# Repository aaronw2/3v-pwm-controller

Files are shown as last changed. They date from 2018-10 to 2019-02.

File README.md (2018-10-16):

# 3v-pwm-controller
An Arduino M0 PWM controller with 3 mosfets designed to perform PWM at 3V
with a 3A 3V supply

This PWM controller provides 3 PWM channels designed to source and sink current.
The PWM signals are configured as an H-bridge with 6 GPIO pins controlling it.
One set of GPIO pins controlls the P-channel mosfets and another set controls
the N-channel mosfets.

Do not pull the P-channel mosfets low while pulling the attached N-channel
mosfet high! This will create a short and cause the 3V power supply to
overheat anb hopefully shut down! Bad things happen!

If you can't control both N and P channels simultaneously, set the P-channel
high and the N-channel low as an intermediate step.

PW0: P-channel = PA02, N-channel = PA05
PW1: P-channel = PA01, N-channel = PA04
PW2: P-channel = PA00, N-channel = PA03

For example, to pull PW0 high and PW1 low and PW2 high impedence (open),
set PA02 low, PA05 low, PA01 high, PA04 high, PA00 high, PA03 low.

The 3V supply is capable of providing up to 3A of current and is designed
to be powered by a 5V supply.

Each PWM channel should be able to handle at least 3A of current at 3V.
The MOSFETs are rated at over 5A each.

J1:
1: +5V
2: +5V
3: PWM0 GNR controlled by pulling PA05 high, +3 controlled by pulling PA02 low
4: PA08
5: PWM1 GND controlled by pulling PA04 high, +3 controlled by pulling PA01 low
6: PA09
7: PWM2 GND controlled by pulling PA03 high, +3 controlled by pulling PA00 low
8: PA10
9: +3V
10: +3V
11: GND
12: GND

J2:
1: D_P (D+) USB signal
2: D_N (D-) USB signal
3: PA22
4: PA21
5: PA19
6: PA18
7: +3V
8: GND

J3:
1: +5V
2: GND

SW1: Reset

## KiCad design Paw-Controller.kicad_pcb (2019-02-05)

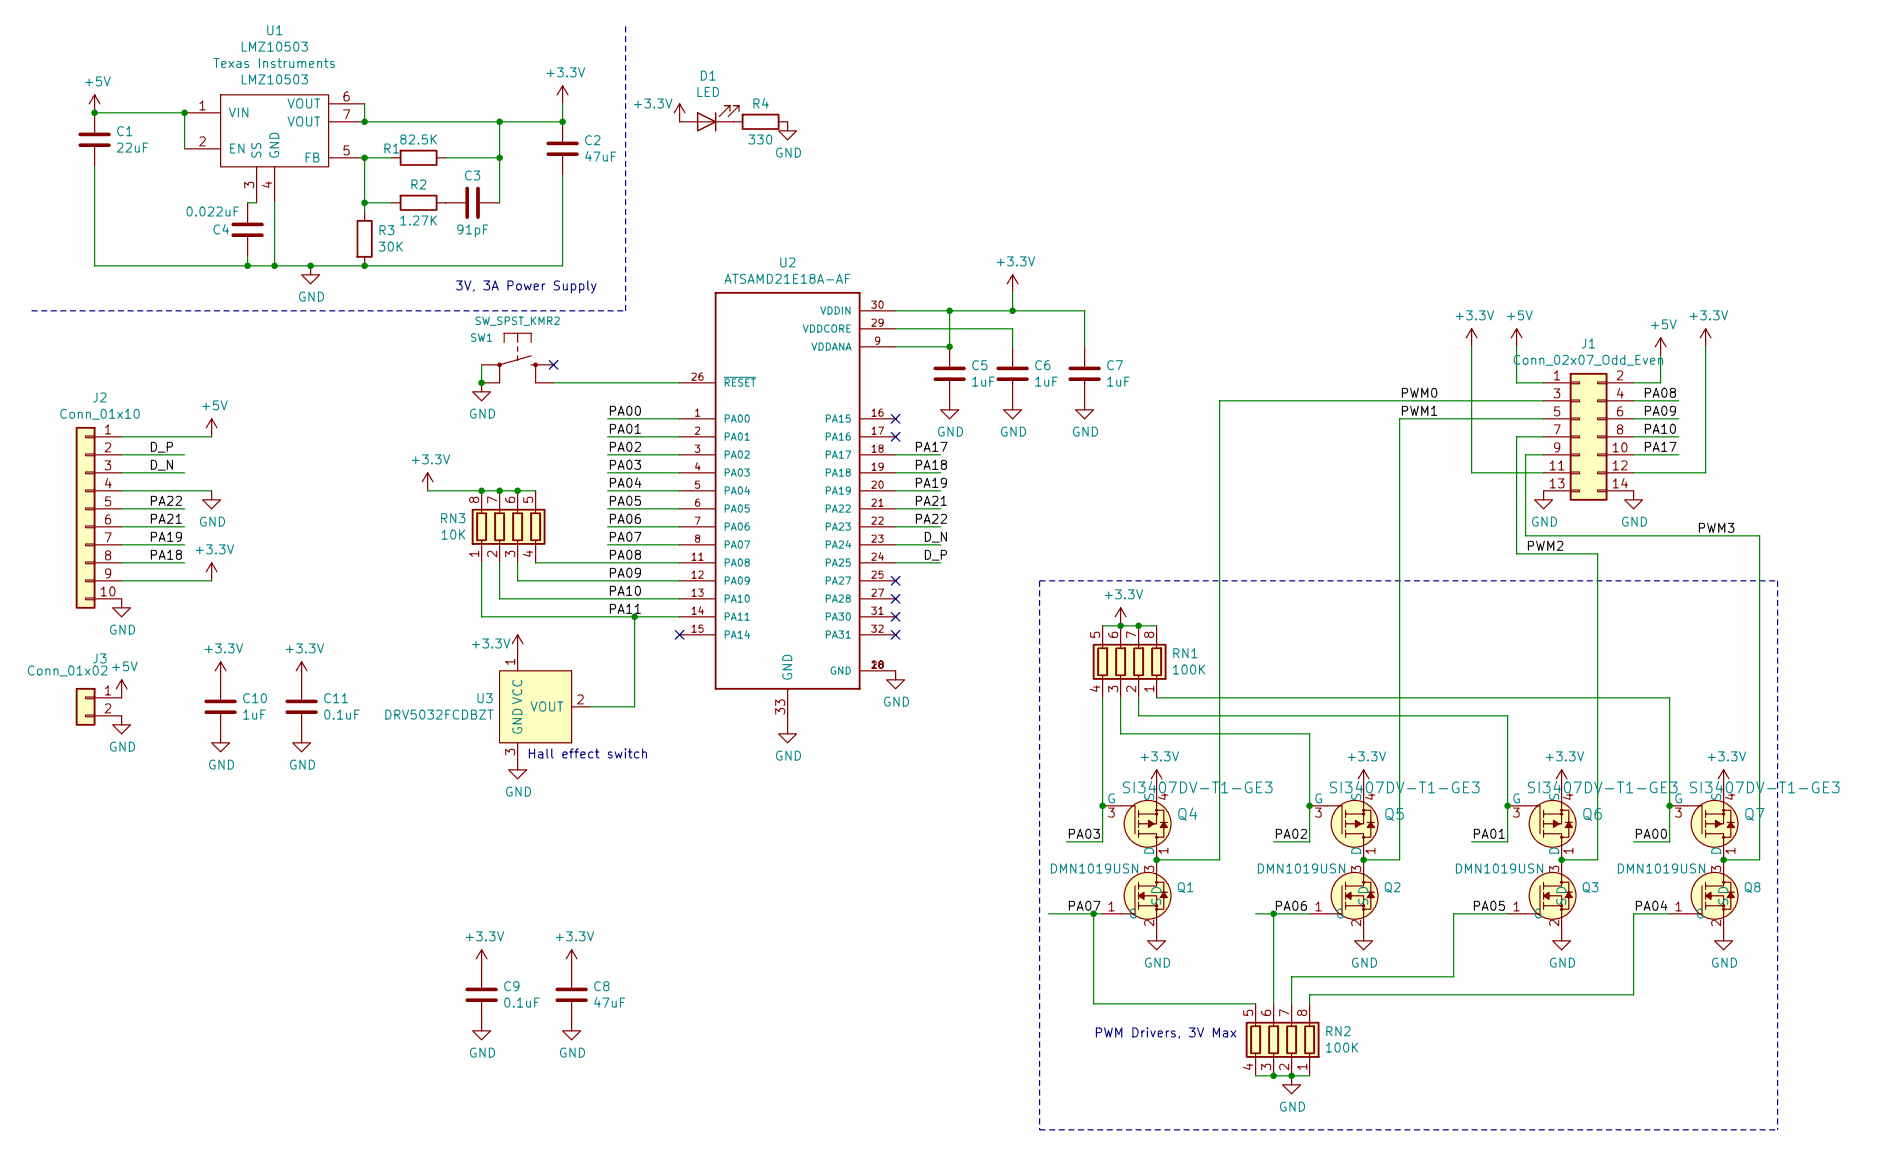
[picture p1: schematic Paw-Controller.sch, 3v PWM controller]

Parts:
C1: 22uF; C_0805_2012Metric
C2, C8: 47uF; C_0805_2012Metric
C3: 91pF; C_0603_1608Metric
C4: 0.022uF; C_0603_1608Metric
C5, C6, C7, C10: 1uF; C_0603_1608Metric
C9, C11: 0.1uF; C_0603_1608Metric
D1: LED; LED_0603_1608Metric
J1: Conn_02x07_Odd_Even; PinHeader_2x07_P2.54mm_Vertical
J2: Conn_01x10; PinHeader_1x10_P2.54mm_Vertical
J3: Conn_01x02; PinHeader_1x02_P2.54mm_Vertical
Q1, Q2, Q3, Q8: DMN1019USN; SOT-23; MPN DMN1019USN-7; Digi-Key_PN DMN1019USN-7DICT-ND
Q4, Q5, Q6, Q7: SI3407DV-T1-GE3; TSOP-6_1.65x3.05mm_P0.95mm; MPN SI3407DV-T1-GE3; Digi-Key_PN SI3407DV-T1-GE3TR-ND
R1: 82.5K; R_0603_1608Metric
R2: 1.27K; R_0603_1608Metric
R3: 30K; R_0603_1608Metric
R4: 330; R_0603_1608Metric
RN1, RN2: 100K; R_Array_Convex_4x0603
RN3: 10K; R_Array_Convex_4x0603
SW1: SW_SPST_KMR2
U1: LMZ10503; TO-PMOD-7_TabPin4; MPN LMZ10503
U2: ATSAMD21E18A-AF; QFN-32-1EP_5x5mm_P0.5mm_EP3.6x3.6mm
U3: DRV5032FCDBZT; SOT-23; MPN DRV5032FCDBZT

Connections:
+3V3: C2.1, C3.1, C5.1, C7.1, C8.1, C9.1, C10.1, C11.1, D1.2 (A), J1.11, J1.12, J2.9, Q4.4 (S), Q5.4 (S), Q6.4 (S), Q7.4 (S), R1.1, RN1.5 (R4.2), RN1.6 (R3.2), RN1.7 (R2.2), RN1.8 (R1.2), RN3.5 (R4.2), RN3.6 (R3.2), RN3.7 (R2.2), RN3.8 (R1.2), U1.6 (VOUT), U1.7 (VOUT), U2.9 (VDDANA), U2.30 (VDDIN), U3.1 (VCC)
+5V: C1.1, J1.1, J1.2, J2.1, J3.1, U1.1 (VIN), U1.2 (EN)
/D_N: J2.3, U2.23 (PA24)
/D_P: J2.2, U2.24 (PA25)
/PA00: Q7.3 (G), RN1.1 (R1.1), U2.1 (PA00)
/PA01: Q6.3 (G), RN1.2 (R2.1), U2.2 (PA01)
/PA02: Q5.3 (G), RN1.3 (R3.1), U2.3 (PA02)
/PA03: Q4.3 (G), RN1.4 (R4.1), U2.4 (PA03)
/PA04: Q8.1 (G), RN2.8 (R1.2), U2.5 (PA04)
/PA05: Q3.1 (G), RN2.7 (R2.2), U2.6 (PA05)
/PA06: Q2.1 (G), RN2.6 (R3.2), U2.7 (PA06)
/PA07: Q1.1 (G), RN2.5 (R4.2), U2.8 (PA07)
/PA08: J1.4, RN3.4 (R4.1), U2.11 (PA08)
/PA09: J1.6, RN3.3 (R3.1), U2.12 (PA09)
/PA10: J1.8, RN3.2 (R2.1), U2.13 (PA10)
/PA11: RN3.1 (R1.1), U2.14 (PA11), U3.2 (VOUT)
/PA17: J1.10, U2.18 (PA17)
/PA18: J2.8, U2.19 (PA18)
/PA19: J2.7, U2.20 (PA19)
/PA21: J2.6, U2.21 (PA22)
/PA22: J2.5, U2.22 (PA23)
/PWM0: J1.3, Q1.3 (D), Q4.1 (D), Q4.2 (D), Q4.5 (D), Q4.6 (D)
/PWM1: J1.5, Q2.3 (D), Q5.1 (D), Q5.2 (D), Q5.5 (D), Q5.6 (D)
/PWM2: J1.7, Q3.3 (D), Q6.1 (D), Q6.2 (D), Q6.5 (D), Q6.6 (D)
/PWM3: J1.9, Q7.1 (D), Q7.2 (D), Q7.5 (D), Q7.6 (D), Q8.3 (D)
GND: C1.2, C2.2, C4.2, C5.2, C6.2, C7.2, C8.2, C9.2, C10.2, C11.2, J1.13, J1.14, J2.4, J2.10, J3.2, Q1.2 (S), Q2.2 (S), Q3.2 (S), Q8.2 (S), R3.2, R4.1, RN2.1 (R1.1), RN2.2 (R2.1), RN2.3 (R3.1), RN2.4 (R4.1), SW1.1, U1.4 (GND), U2.10 (GND), U2.28 (GND), U2.33 (GND), U3.3 (GND)
unnamed: C3.2, R2.1
unnamed: C4.1, U1.3 (SS)
unnamed: C6.1, U2.29 (VDDCORE)
unnamed: D1.1 (K), R4.2
unnamed: R1.2, R2.2, R3.1, U1.5 (FB)
unnamed: SW1.2 (S), U2.26 (~RESET~)

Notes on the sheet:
3V, 3A Power Supply
PWM Drivers, 3V Max
Hall effect switch

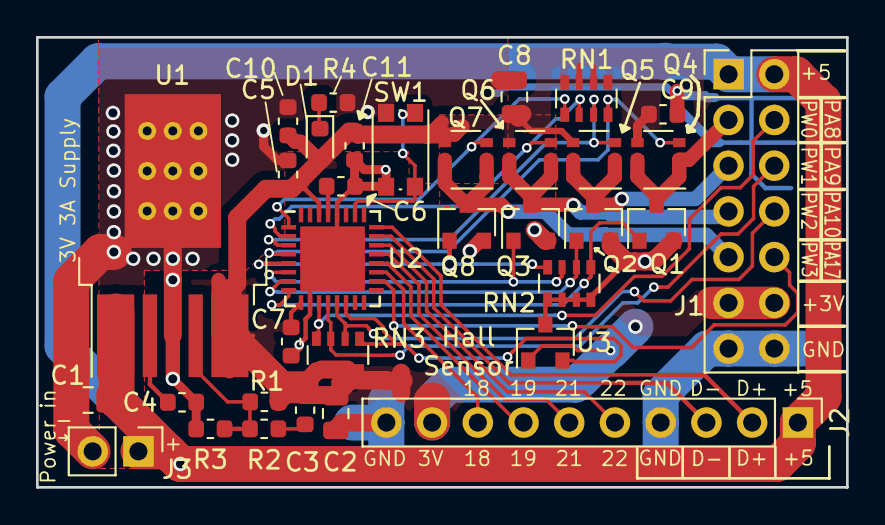
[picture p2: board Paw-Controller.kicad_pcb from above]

Board: 2 copper layers, 45.0 x 25.0 mm, 34 parts (0 on the bottom side), 32 nets.

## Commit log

2018-10-15 Initial checkin of Arduino M0 based PWM controller.
    This PWM controller provides 3 PWM channels designed to sink current.
    Due to the back EMF protection diodes, do not exceed 5v.
    The 3V supply is capable of providing up to 3A of current and is designed
    to be powered by a 5V supply.
    Each PWM channel should be able to handle at least 3A of current at up to 5V.
    The MOSFETs are rated at over 8A each.
    J1:
    1: +5V
    2: +5V
    3: PWM0 connected to PA00
    4: PA08
    5: PWM1 connected to PA01
    6: PA09
    7: PWM2 connected to PA02
    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
    [Paw-Controller.kicad_pcb, Paw-Controller.sch]
2018-10-15 Added missing PWM labels.
    [Paw-Controller.kicad_pcb, Paw-Controller.sch]
2018-10-16 Version 2.0 converts each PWM channel to use an H-bridge.
    This allows the controller to be able to drive a 3V brushless motor. The
    M0 processor is capable of generating the timing for the motors, though at
    this time I don't know if it works with 6 GPIO pins or only with three.
    Six was chosen so that a PWMs can be set to a high impedence state. This
    is useful in the case where multiple brushed motors are attached between either
    +3v or ground and the PWM pin, though the alternative is to just pull the PWM
    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
    [Paw-Controller.kicad_pcb, Paw-Controller.sch]
2019-01-26 Fixed solder mask clearance.
    [Paw-Controller.kicad_pcb, Paw-Controller.sch]
2019-01-30 Fixed P-CH mosfets and changed to more readily available mosfet.
    [Paw-Controller.kicad_pcb, Paw-Controller.sch]
2019-01-30 Add another push/pull channel
    This adds a 4th push/pull channel and exports PA17 to J1.
    Due to the increase in board size, two more pins were added to J2,
    an additional +5 and ground pin for USB.
    Updated to version 2.2.0
    [Paw-Controller.kicad_pcb, Paw-Controller.sch]
2019-02-05 Fixed silkscreen and solder mask.
    [Paw-Controller.kicad_pcb]

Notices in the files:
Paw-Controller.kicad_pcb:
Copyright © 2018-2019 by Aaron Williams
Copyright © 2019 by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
